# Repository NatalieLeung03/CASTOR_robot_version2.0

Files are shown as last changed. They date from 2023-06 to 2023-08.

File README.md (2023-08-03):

# Castor

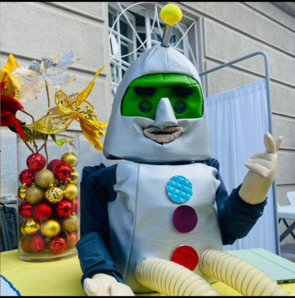
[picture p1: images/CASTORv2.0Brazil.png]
castor


(labeled diagram with all parts)

Head

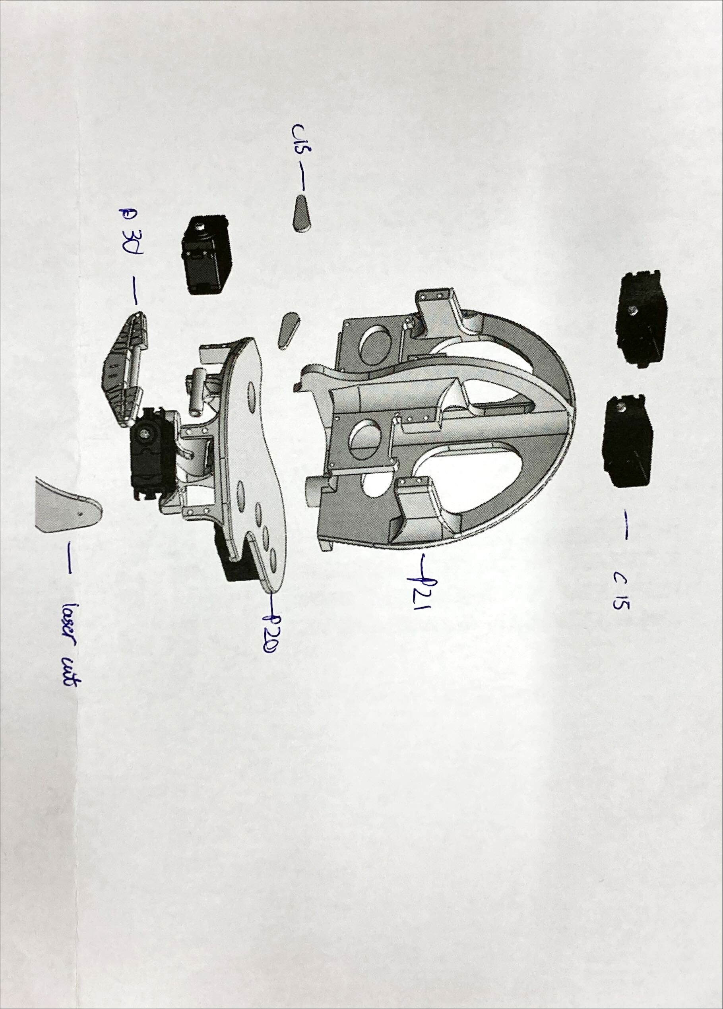
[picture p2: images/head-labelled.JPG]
head


Arm

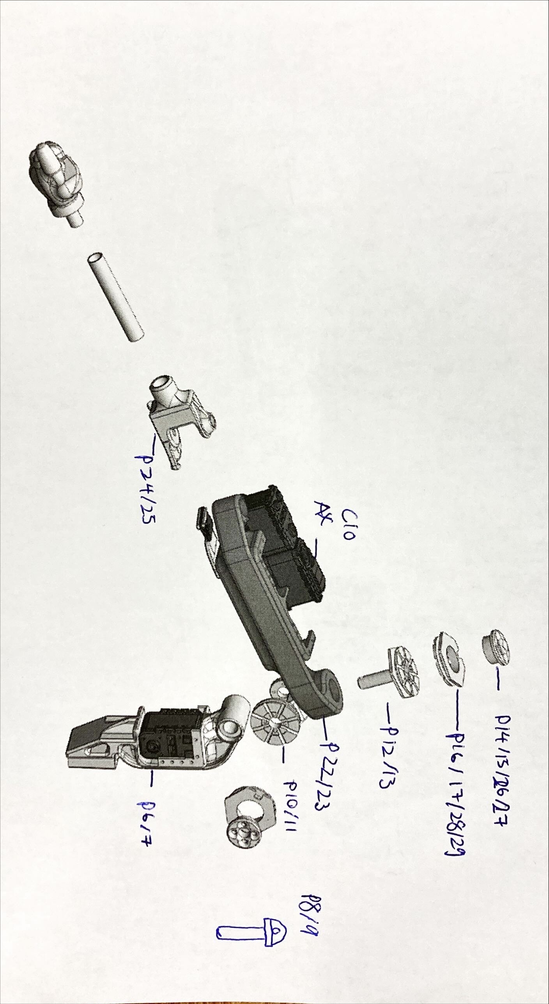
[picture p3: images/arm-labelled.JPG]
arm


Base

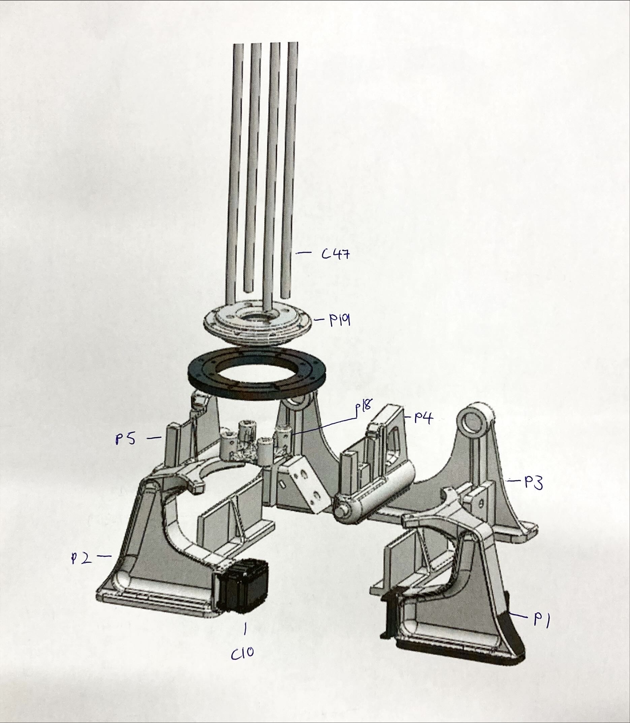
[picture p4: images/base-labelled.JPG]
base


## 3D printing
3D printing parts STL files
[castor 3D print](https://github.com/NatalieLeung03/castor/tree/main/castor-design-master)

parts 1-29 in PLA or ABS plastics, part 30 in TPU plastic or flex resin

### special parts
In version 2.0, parts 6,7, 10, 11, 16, 17, 28, 29 are changed. Pieza boca can be 3D printed or laser-cutted for the mouth-piece. 120mm bearing can also be printed if it is not available in the country.

[Bearing](https://github.com/NatalieLeung03/castor/tree/main/castor-design-master/bearing): 
- bolitas_estatica X 18    #static balls
- bolitas_rodamiento X 18  #bearing balls
- Rod_soporte X 1          #rod support

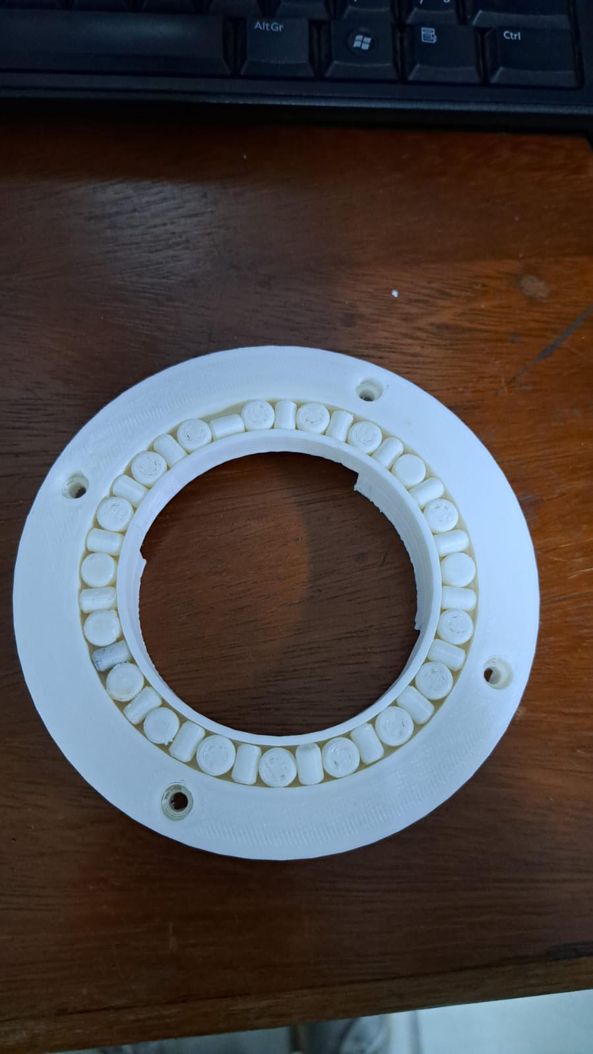
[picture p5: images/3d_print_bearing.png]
bearing


To assemble it, place a static piece and a spherical piece intercalated as in the image, then carefully place 3d printing piece number 19 on top to cover the small pieces. Small pieces in the bearing are not supposed to move, it is supposed that the other piece roll over the bearing with those pieces.

We encountered a problem when doing these. Since support material is used when printing rod_soporte, the balls don't fit in perfectly and we will need to clean them with sandpaper. However, it is easy to overdo, so we ended up with too much space in the bearing and more balls are needed.

Different methods are going to be tested out soon.

[Bioinspired arm module](https://github.com/NatalieLeung03/castor/tree/main/castor-design-master/bioinspired%20arm%20module):
- poleaax12 for the ax-12a motors
- poleamx106 for the mx-106t motors

Depending on the version, each motor on the arms needs one pole. Version 1.0 will need 6 poleaax12, and Version 2.0 needs 4 poleaax12 + 2 poleamx106.

[Base](https://github.com/NatalieLeung03/castor/tree/main/castor-design-master/base):
- base piece
- union nervio

### skeleton
For parts 1-7,10,11,19-25, the infill is 30% with a wall thickness of 4 passes as seen in Fig. 1. 
For parts 8,9,12-18,26-29, the percentage of infill will be 80 to 100% because these parts require high rigidity for proper operation. On the other hand, for the printing of part 30 the use of filaflex material of 700% elongation is required. The printing characteristics for this part depend on the temperature characteristics and conditions of each machine (Recommendation: perform a temperature and calibration test for these elastic materials).

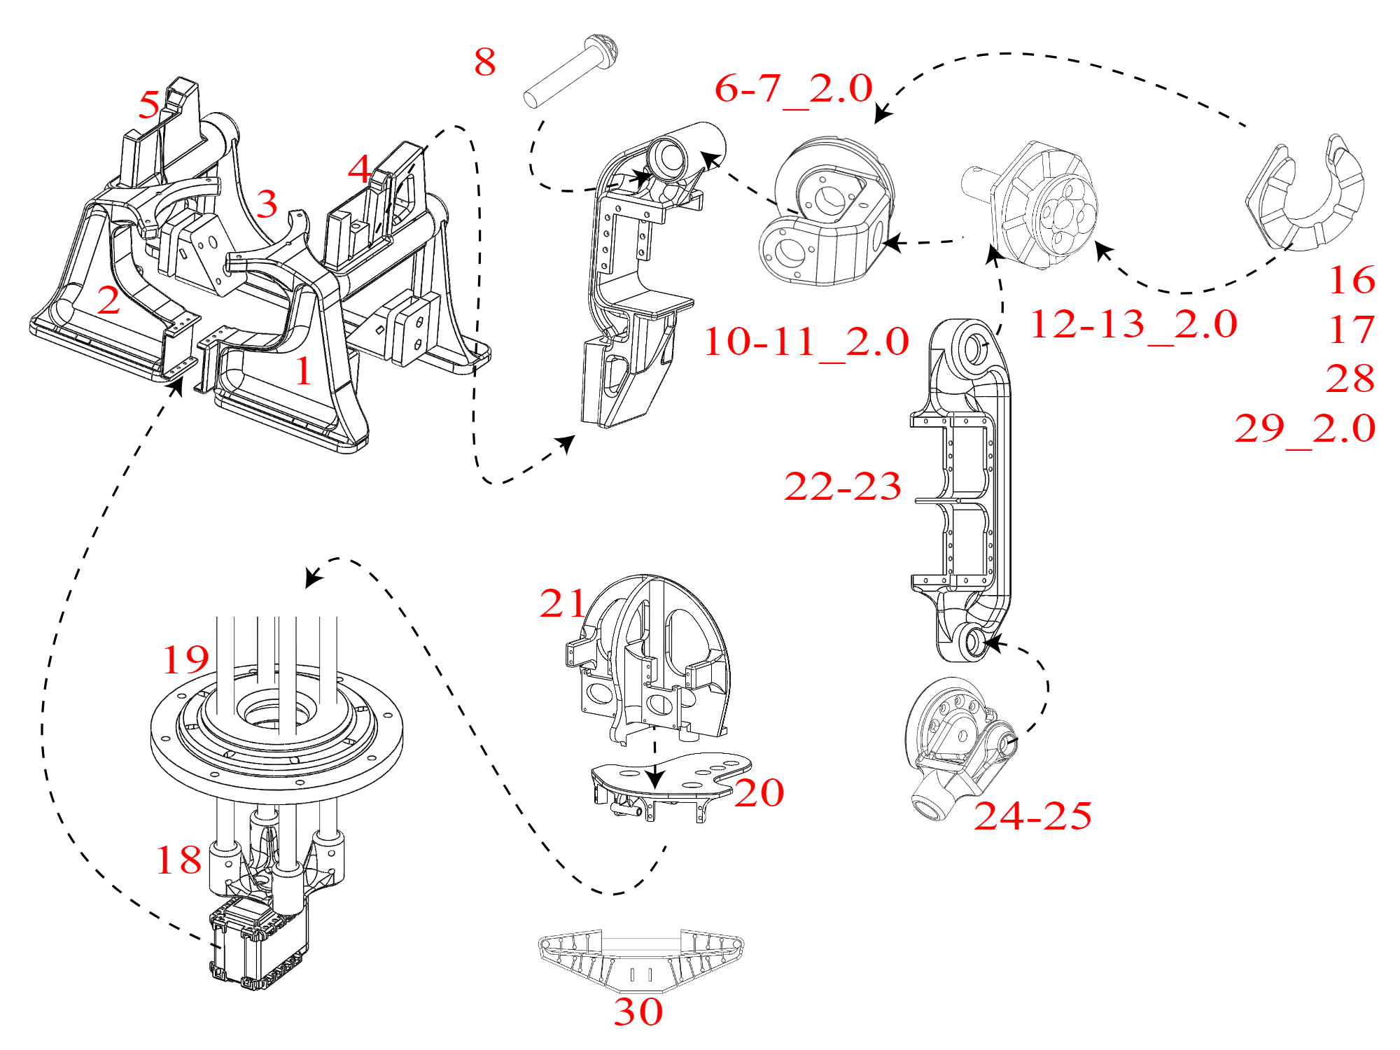
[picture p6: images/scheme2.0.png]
scheme


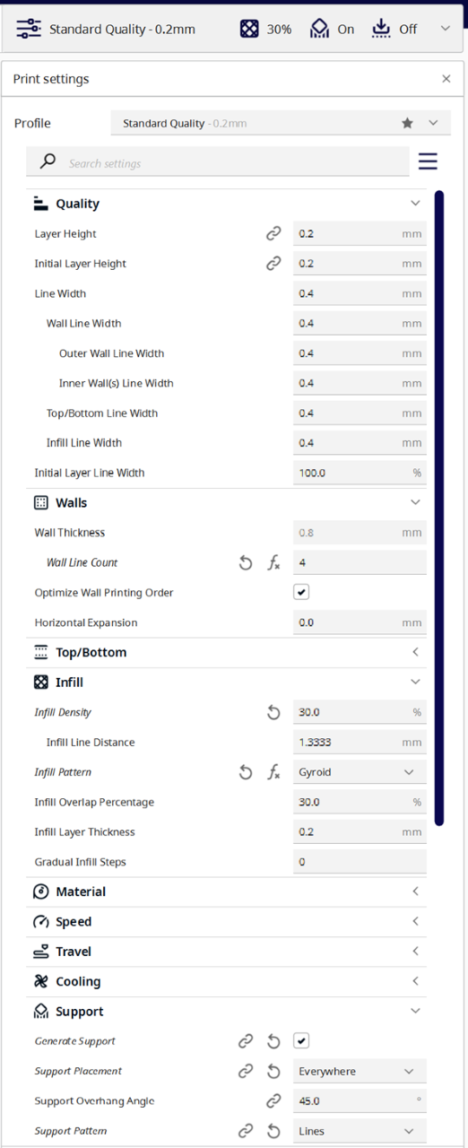
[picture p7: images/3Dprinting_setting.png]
setting


Fig1

## Electronics parts
Version 2.0 only needs 1 Raspberry Pi, Pi 4 or 3 model B+.

PWM PCA 9685

Adafruit eyes 11 pins, LCD display of 7-8 pins

## Components
5 Dynamixel AX-12A + 2 Dynamixel MX-106T -> 7 Dynamixel AX-12A 
(Any other amplifier with 10W and stereo input)

## Motors 
5 servo motors on castor head (2 eyebrows, 2 corners of mouth, 1 mouth piece)
(image of CASTOR head)

7 Dynamixel AX-12A 

- Neck motor ID: 1
- Right Shoulder Roll motor ID: 2
- Right Shoulder Pitch motor ID: 3
- Right Elbow Pitch motor ID: 4
- Left Shoulder Roll motor ID: 5
- Left Shoulder Pitch motor ID: 6
- Left Elbow Pitch motor ID: 7

## Screws
- M4 hex 3cm				x2			
- M3 star 1cm				x21
- M3 hex neck 2cm			x4
- Dynamixel pulley screws		x24     #m4?
- Dynamixel neck screws			x4      #m4?
- Base screws				x4              #m4?
- M3 nuts				x30
- M4 nuts				x20
- Piston screws				x8            #they are included in the piston kit

## Outfit and infill
### Outfit
[sewing pattern](https://github.com/NatalieLeung03/castor/tree/main/Sewing%20Patterns) -- need dimensions

Sewing Pattern	Materials

1	Leather - Green Color

2	Leather - Green Color

3	Leather - Metallic Color

4	Leather - Metallic Color

5	Leather - Metallic Color

6	Leather - Metallic Color

7	Leather - Metallic Color

8	Leather - Metallic Color

9	Leather - Metallic Color

10	Leather - Metallic Color

11	Stretch Fabric - M. Navy Color

12	Leather - Metallic Color

13	Stretch Fabric - M. Navy Color

14	Stretch Fabric - M. Navy Color

15	Leather - Beige Color

16	Leather - Metallic Color

17	Leather - Metallic Color

18	Leather - Metallic Color

19	Leather - Metallic Color

20	Leather - Metallic Color

21	Leather - Metallic Color

22	Leather - Metallic Color

23	Leather - Black Color

24	Polyethylene Foam 0.5''

25	Polyethylene Foam 0.5''

### Infill
no pattern or template at the moment, only images
- Polyethylene foam (chest)
- Foam

## Power and connect
### Electronic systems and sub-system overview
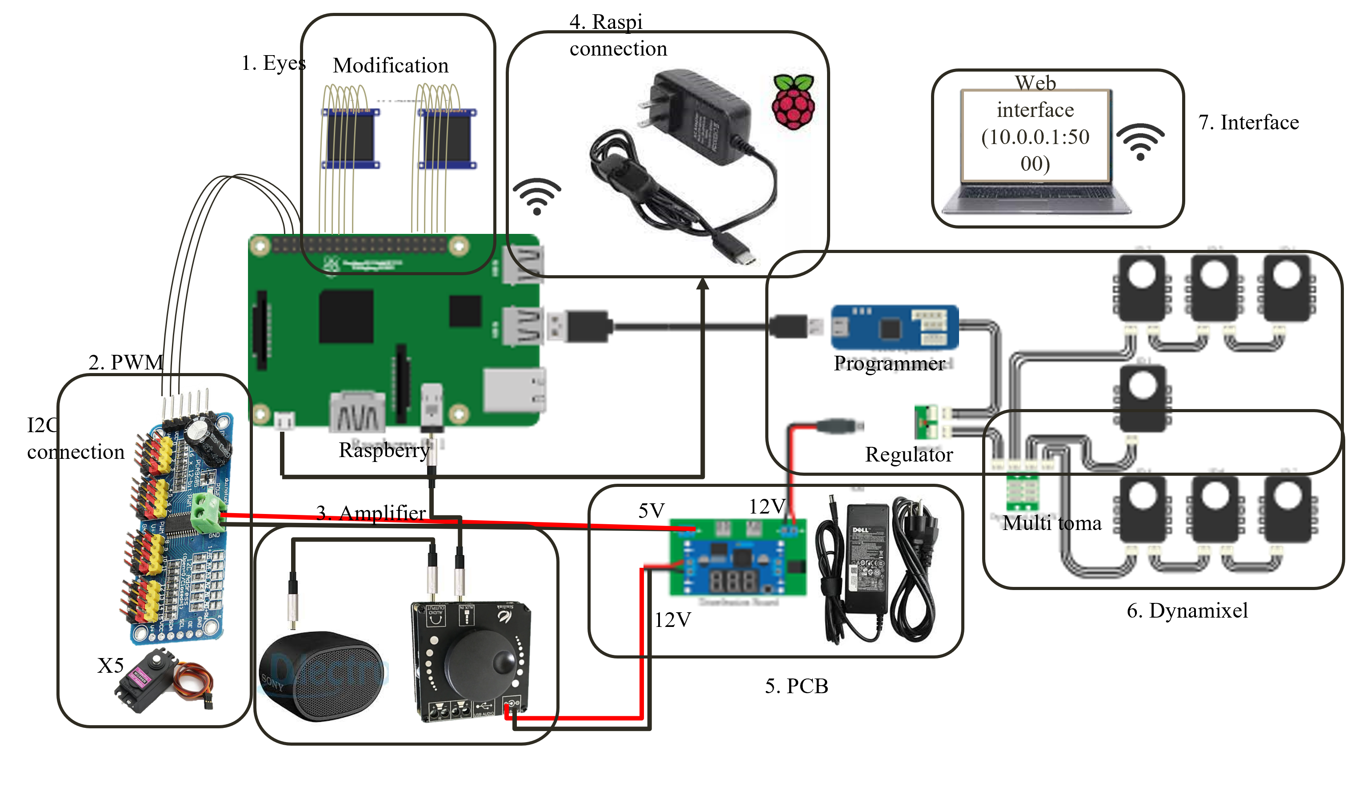
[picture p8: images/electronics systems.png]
electsys


### PCB and power up CASTOR
PCB is needed for the LM2956, with few other components.

CASTOR PCB is from version 1.0, created using Eagle, including schematic and board files.

Power_PCB_(LM2596_with_display) and Power_PCB_(LM2596_without_display) are version 2.0, created using Altium, including all the Gerber files.

[temp link to preview Power_PCB_(LM2596_with_display)](https://www.altium.com/viewer?token=yrjcqPPWnUKv%2FRbAUB7A97Gh)

## Code
### Web interface
Here is a shorter version of the web interface compared to version 1, and in English. 
[castor 3D print](https://github.com/NatalieLeung03/castor/tree/main/web_interface_english_int) updated 18:14 27/07/23, valid for 2 days

Future goal: improve code into better structure and implement Google speech-to-text and text-to-speech and ChatGPT API into it. In order to have a smoother conversation.

# License
[read license](https://github.com/NatalieLeung03/castor/blob/main/LICENSE.txt)

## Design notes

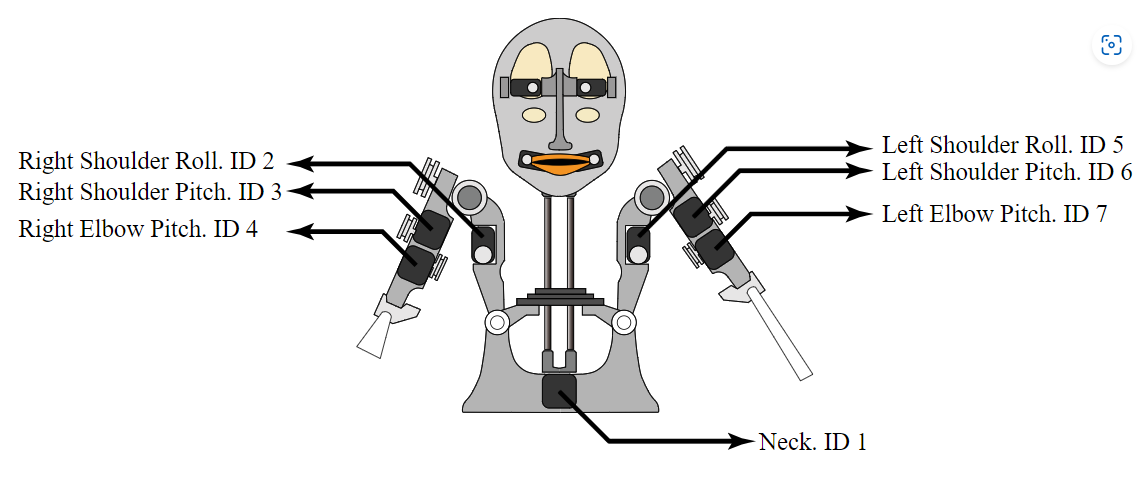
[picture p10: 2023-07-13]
images/motors config.png

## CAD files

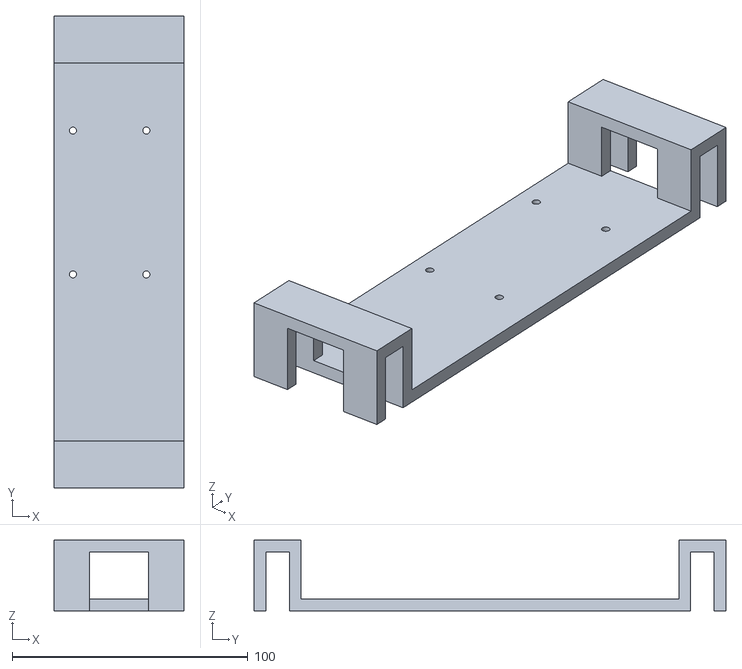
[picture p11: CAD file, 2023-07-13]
castor-design-master/base/Base_piece.stl
55.0 x 200.0 x 30.0

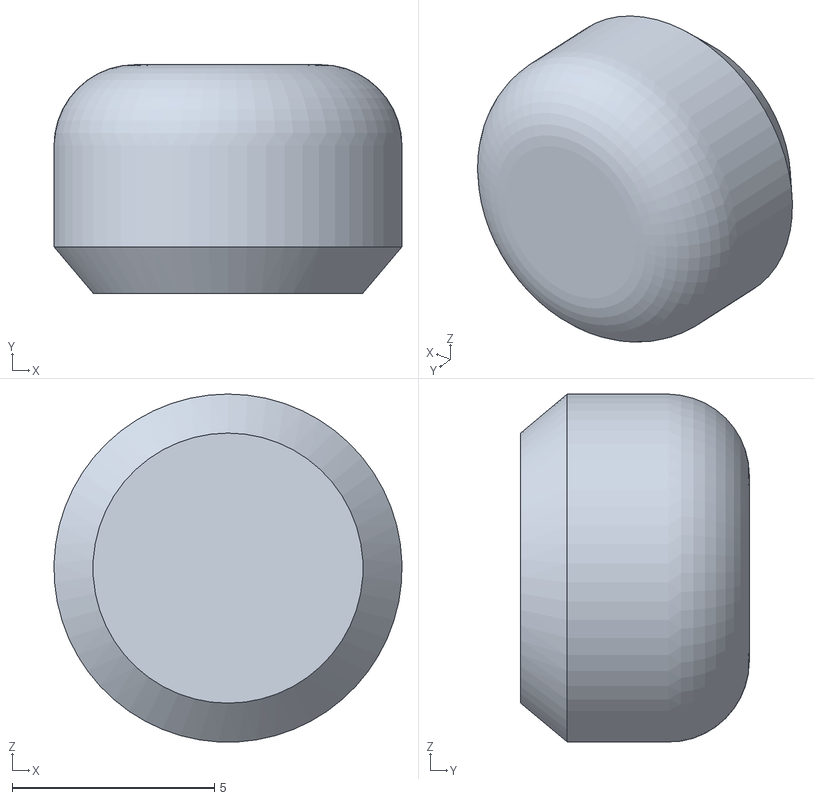
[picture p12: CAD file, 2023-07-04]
castor-design-master/bearing/bolitas_estatica.stl
8.60 x 5.65 x 8.59

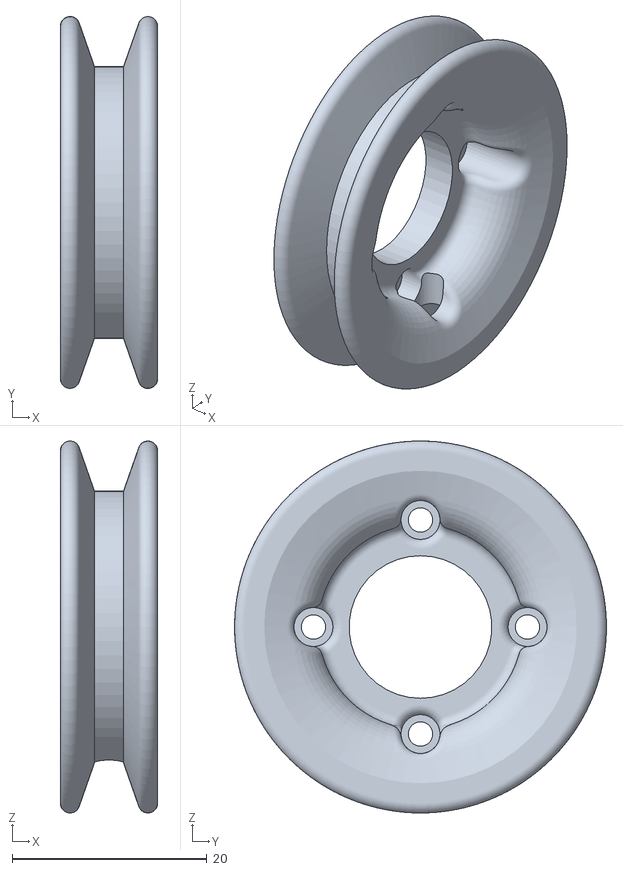
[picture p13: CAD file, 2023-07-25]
castor-design-master/bioinspired arm module/poleamx106.STL
10.0 x 38.2 x 38.2

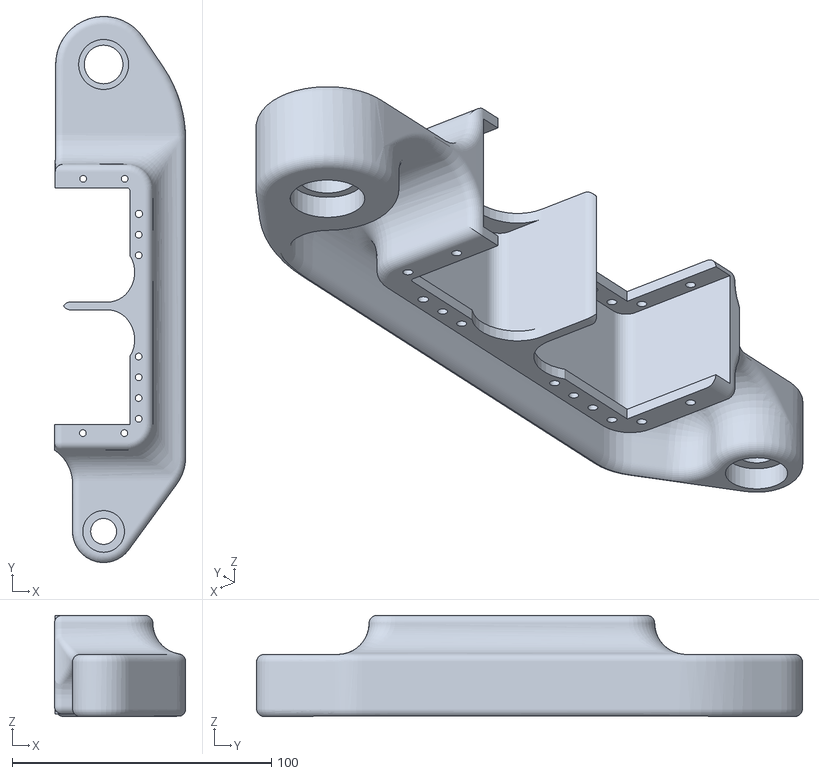
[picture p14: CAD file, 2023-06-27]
castor-design-master/main body/23.STL
50.6 x 210.5 x 39.0

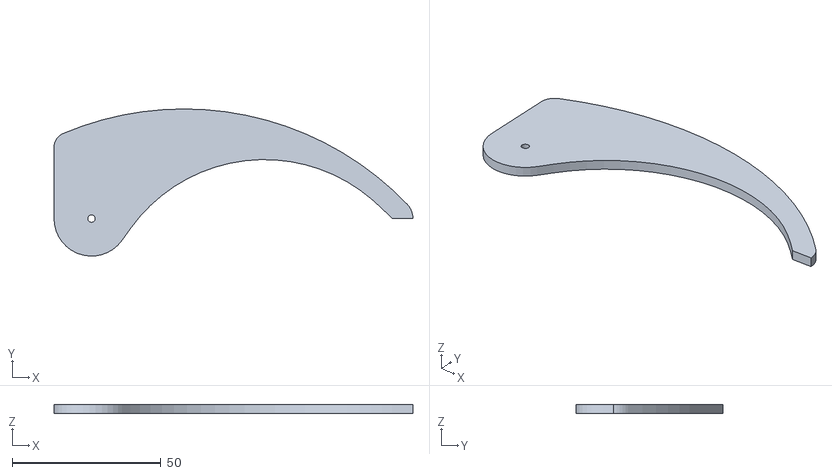
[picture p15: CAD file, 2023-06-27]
castor-design-master/mouthpiece/pieza boca.STL
120.6 x 49.4 x 3.00

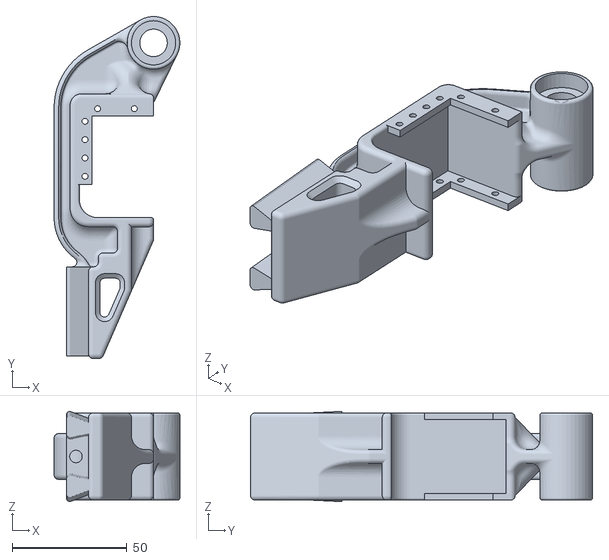
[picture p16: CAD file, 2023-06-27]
castor-design-master/v1.0 for reference/6-7.STL
54.9 x 149.1 x 39.4

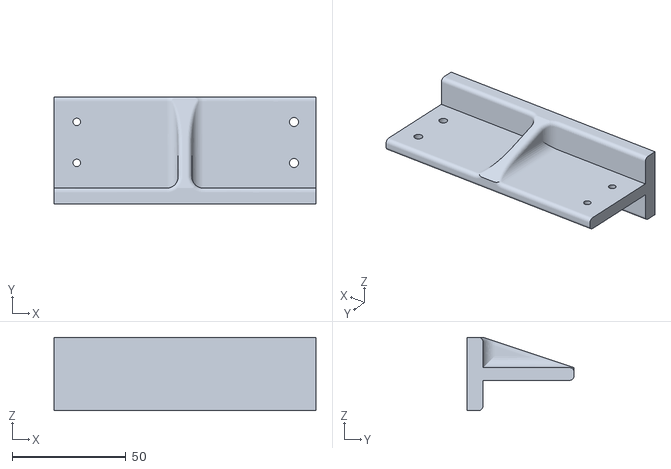
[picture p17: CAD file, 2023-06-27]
castor-design-master/base/union nervio.STL
115.0 x 47.0 x 32.3

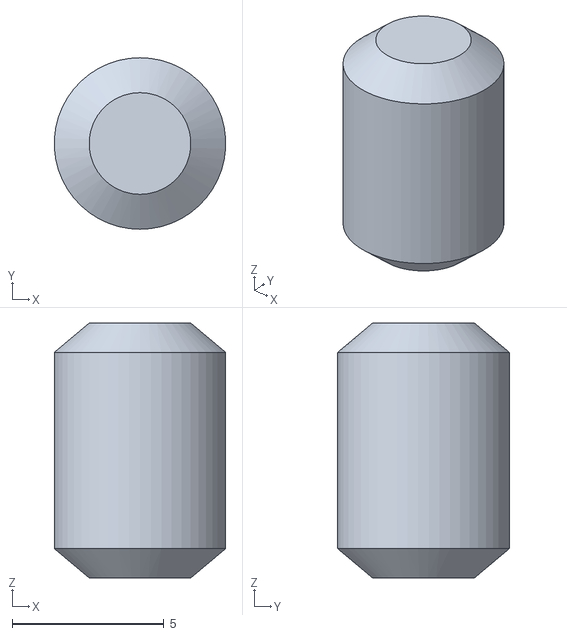
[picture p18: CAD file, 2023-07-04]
castor-design-master/bearing/bolitas_rodamiento.stl
5.64 x 5.65 x 8.40

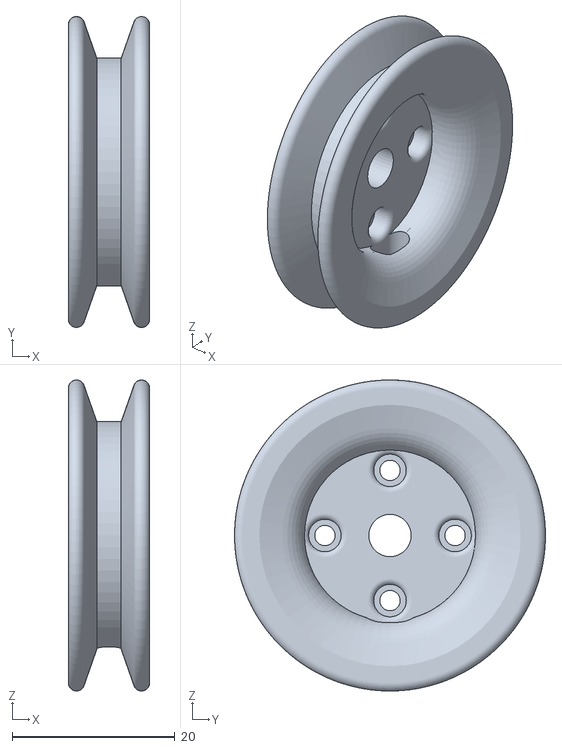
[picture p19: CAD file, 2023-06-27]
castor-design-master/bioinspired arm module/poleaax12.STL
10.0 x 38.2 x 38.2

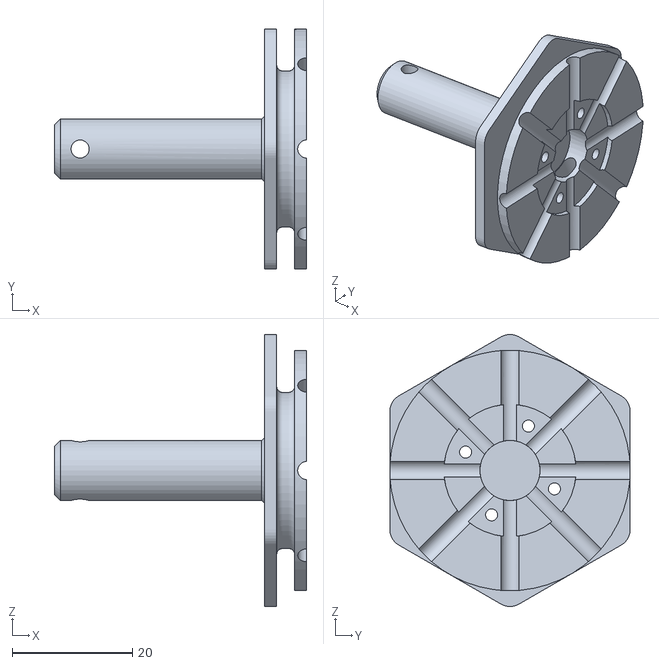
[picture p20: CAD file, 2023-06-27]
castor-design-master/main body/12-13.STL
42.0 x 40.0 x 45.3

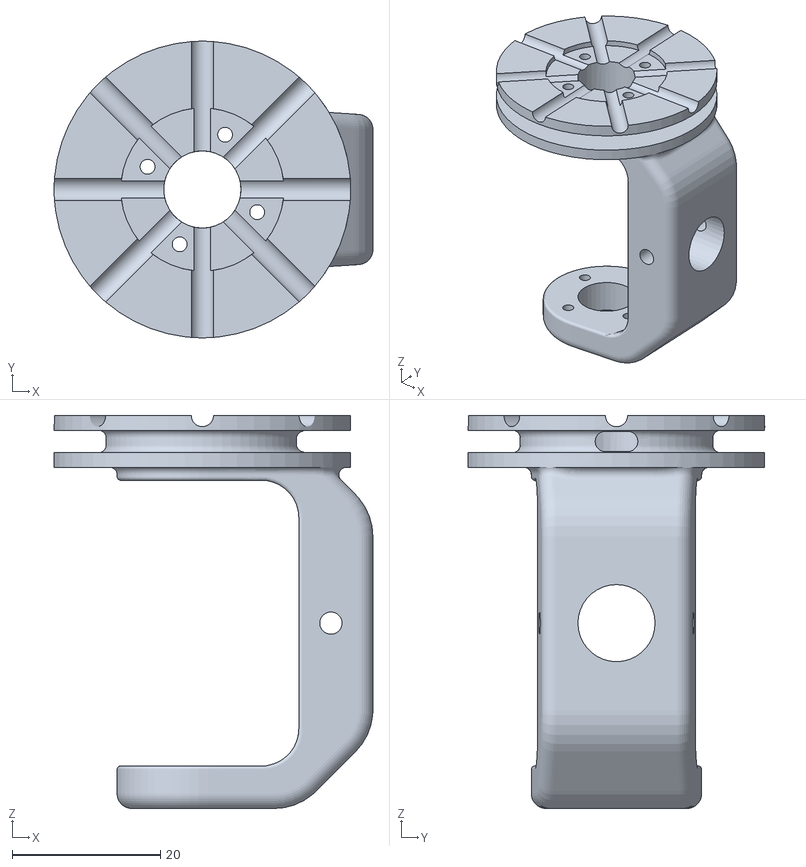
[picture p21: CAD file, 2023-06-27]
castor-design-master/v1.0 for reference/10-11.STL
43.0 x 40.0 x 53.0

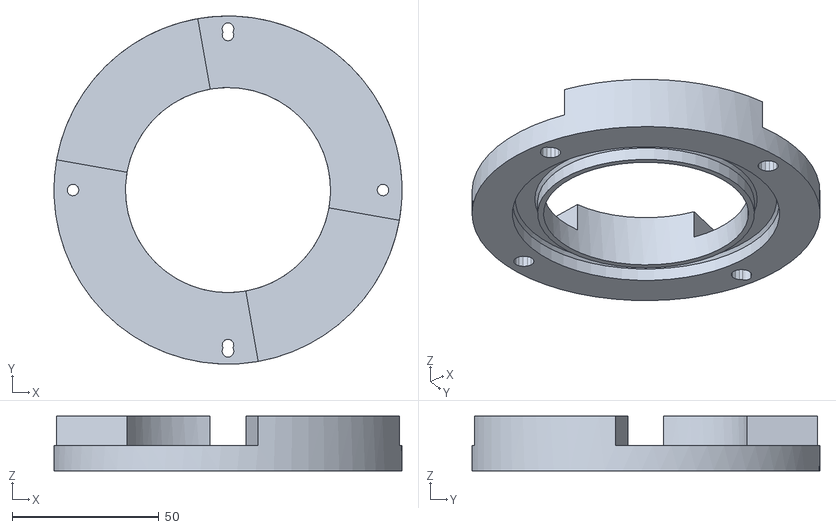
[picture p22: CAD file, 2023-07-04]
castor-design-master/bearing/Rod_soporte.stl
118.8 x 118.8 x 18.6

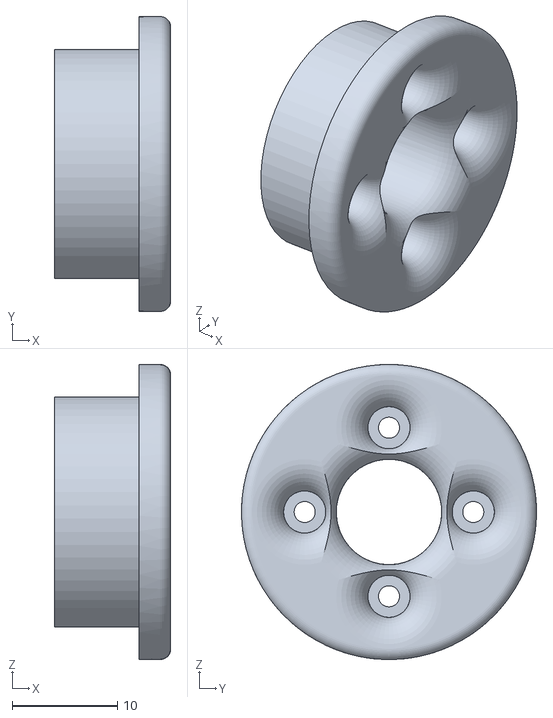
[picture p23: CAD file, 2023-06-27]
castor-design-master/main body/14-15-26-27.STL
11.1 x 28.0 x 28.0

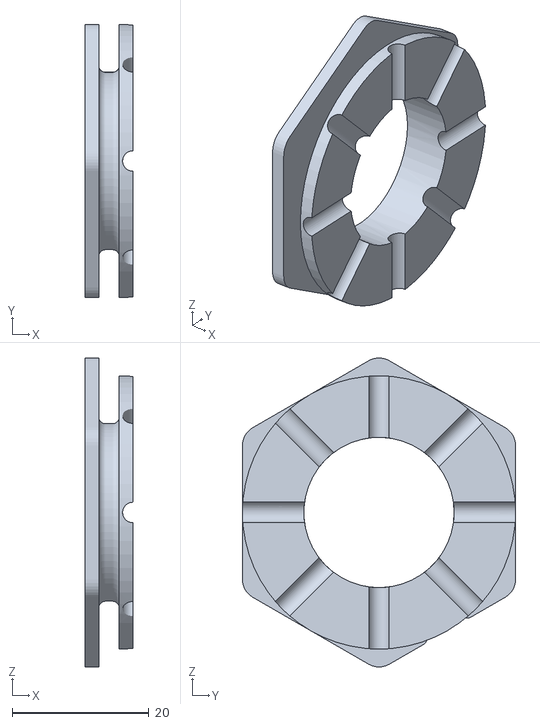
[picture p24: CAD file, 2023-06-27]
castor-design-master/v1.0 for reference/16-17-28-29.STL
7.00 x 40.0 x 45.3

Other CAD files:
castor-design-master/main body/21.STL
castor-design-master/main body/22.STL
castor-design-master/main body/1.STL
castor-design-master/main body/4.STL
castor-design-master/main body/10-11_2.0.STL
castor-design-master/main body/16-17-28-29_2.0.STL
castor-design-master/main body/18.STL
castor-design-master/main body/19.STL
castor-design-master/main body/2.STL
castor-design-master/main body/20.STL
castor-design-master/main body/24.STL
castor-design-master/main body/25.STL
castor-design-master/main body/3.STL
castor-design-master/main body/30.STL
castor-design-master/main body/5.STL
castor-design-master/main body/6-7_2.0.STL
castor-design-master/main body/8-9.STL

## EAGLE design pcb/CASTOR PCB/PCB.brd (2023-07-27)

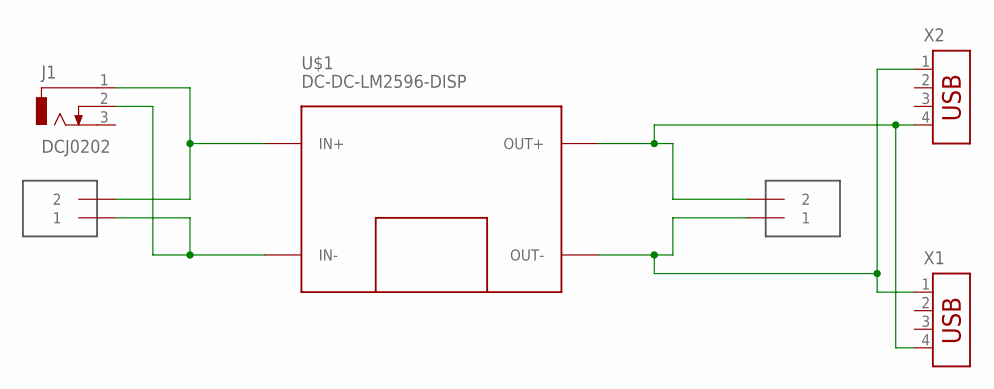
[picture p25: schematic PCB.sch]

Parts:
J1: DCJ0202
U$1: DC-DC-LM2596-DISP
U$2, U$3: TERMINAL_2P; KF301-2P
X1, X2: USB-787616; USB

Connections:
unnamed: J1.1, U$1.IN+, U$2.2
unnamed: J1.2, U$1.IN-, U$2.1
unnamed: U$1.OUT+, U$3.2, X1.4, X2.4
unnamed: U$1.OUT-, U$3.1, X1.1, X2.1

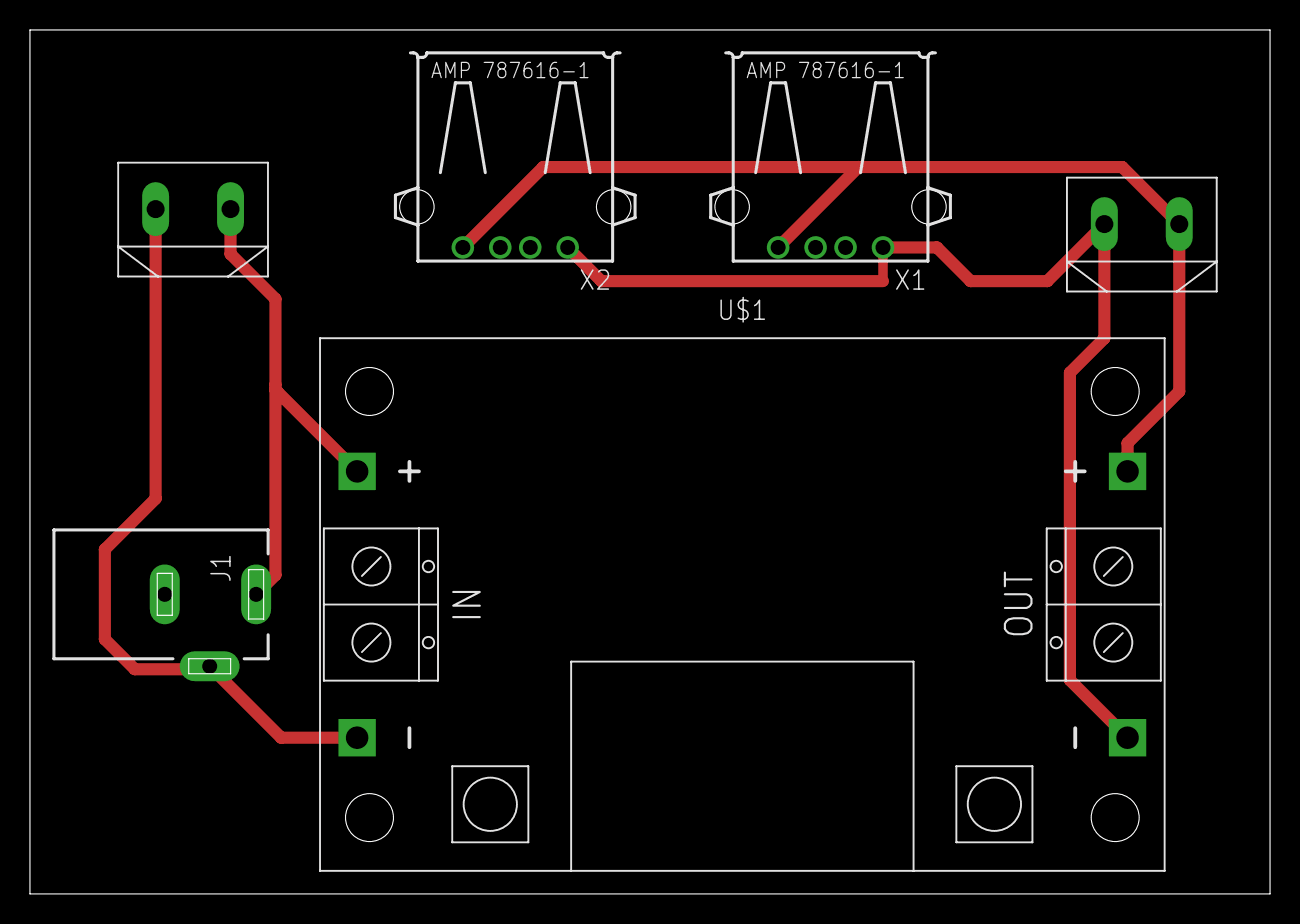
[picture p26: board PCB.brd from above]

Board: 2 copper layers, 82.8 x 57.7 mm, 6 parts (0 on the bottom side), 4 nets.

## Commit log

2023-06-27 Add files via upload
    castor-design-3Dprinting
    [1.STL, 10-11.STL, 10-11_2.0.STL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]
2023-07-27 Update README.md with PCB

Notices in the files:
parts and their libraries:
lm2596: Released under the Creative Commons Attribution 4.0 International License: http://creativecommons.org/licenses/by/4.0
